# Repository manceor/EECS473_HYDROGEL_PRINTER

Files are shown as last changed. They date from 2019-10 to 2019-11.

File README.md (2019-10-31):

# Software Setup Guide

## Flashing the ATmega1284P through USB

To program the ATmega1284P, install download AVROSP.

This guide assumes that you have AVROSP added to your PATH.

1) When you first plug in the board

2) Hold RESET and SW0

3) Let go of RESET

4) Let go of SW0

5) In the terminal, enter the command "mode comx baud=57600 parity=n data=8".
    Replace the "x" in "comx" with the COM port that your board is plugged into.
    This can be found in the "Device Manager" on windows (AVR only supports COM ports 1-8)

6) In the folder where your .hex file is, run the following command:
    "AVROSP -dATmega1284P -cCOMx -pf -vf -if "filename.hex" -e".

## Setting up Atmel Studio for board programming

Install Atmel Studio 7

From fresh code:
Download TH3D Firmware <https://www.th3dstudio.com/knowledgebase/th3d-unified-firmware-package/>
Unzip into a folder of your choice, now referred to as "%TH3D DIRECTORY%"

1) New -> Project -> Create Project From Arduino Sketch

2) Create a new folder somewhere and select it

3) Sketch File:"%TH3D DIRECTORY%\TH3DUF_R2\Firmware\TH3DUF_R2\TH3DUF_R2.ino"

4) Arduino IDE Path: "%TH3D DIRECTORY%\TH3DUF_R2\Windows Arduino\"

5) To find the Marlin Code: see Arduino Core -> include -> variants

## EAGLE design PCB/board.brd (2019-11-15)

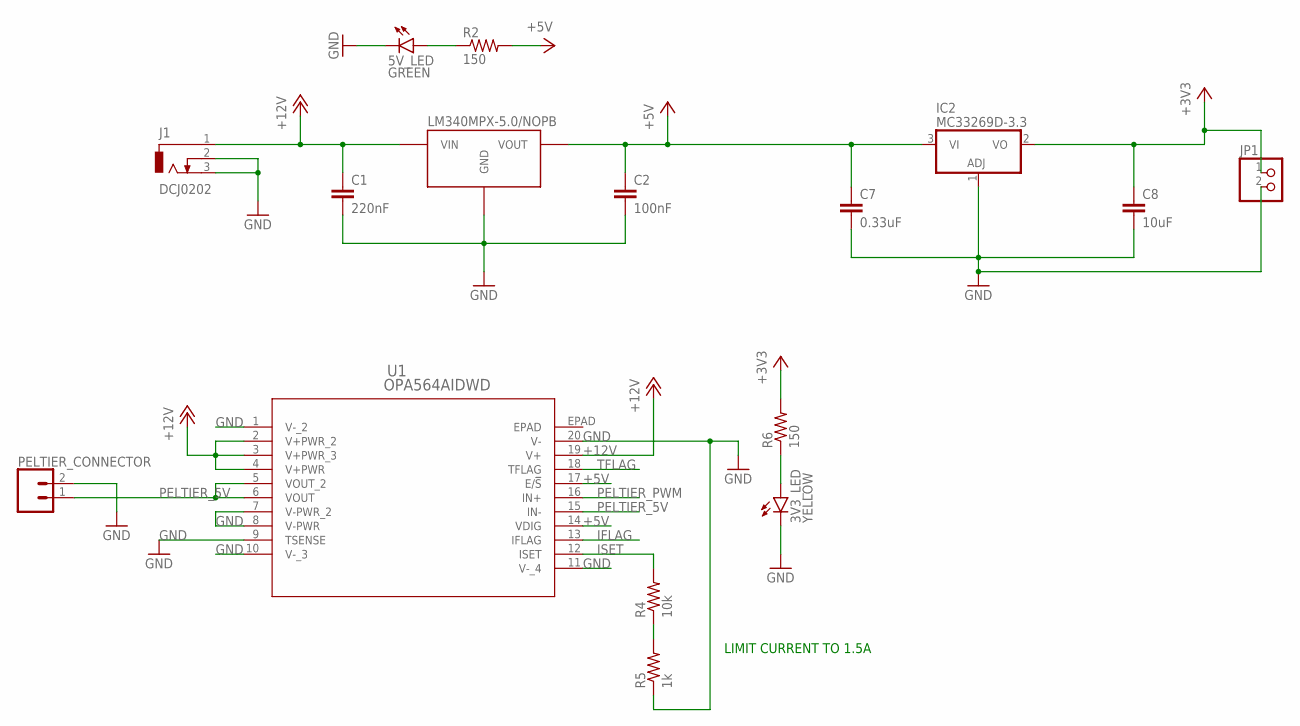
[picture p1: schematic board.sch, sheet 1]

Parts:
3V3_LED: YELLOW; CHIP-LED0603
5V_LED: GREEN; CHIP-LED0603
C1: 220nF; C0805
C2: 100nF; C0805
C7: 0.33uF; C0805
C8: 10uF; C0805
IC2: MC33269D-3.3; DPACK
J1: DCJ0202
JP1: PINHD-1X2; 1X02
LDO1: LM340MPX-5.0/NOPB; SOT-223
PELTIER_CONNECTOR: CONN_025MM; SCREWTERMINAL-5MM-2
R2, R6: 150; R0603
R4: 10k; R0603
R5: 1k; R0603
U1: OPA564AIDWD; DWD20_4P62X3P56

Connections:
+3V3: C8.1, IC2.2 (VO), JP1.1, R6.2
+5V: C2.1, C7.1, IC2.3 (VI), LDO1.P$3 (VOUT), R2.2, U1.14 (VDIG), U1.17 (E/!S); also elsewhere on the board
+12V: C1.1, J1.1, LDO1.P$1 (VIN), U1.2 (V+PWR_2), U1.3 (V+PWR_3), U1.4 (V+PWR), U1.19 (V+); also elsewhere on the board
GND: 3V3_LED.C, 5V_LED.C, C1.2, C2.2, C7.2, C8.2, IC2.1 (ADJ), J1.2, J1.3, JP1.2, LDO1.P$2 (GND), LDO1.P$4 (GND), PELTIER_CONNECTOR.2, R5.1, U1.1 (V-_2), U1.7 (V-PWR_2), U1.8 (V-PWR), U1.9 (TSENSE), U1.10 (V-_3), U1.11 (V-_4), U1.20 (V-); also elsewhere on the board
IFLAG: U1.13 (IFLAG); also elsewhere on the board
ISET: R4.2, U1.12 (ISET)
unnamed: 5V_LED.A, R2.1
unnamed: R4.1, R5.2
unnamed: 3V3_LED.A, R6.1
PELTIER_5V: PELTIER_CONNECTOR.1, U1.5 (VOUT_2), U1.6 (VOUT), U1.15 (IN-)
PELTIER_PWM: U1.16 (IN+); also elsewhere on the board
TFLAG: U1.18 (TFLAG); also elsewhere on the board

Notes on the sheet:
LIMIT CURRENT TO 1.5A

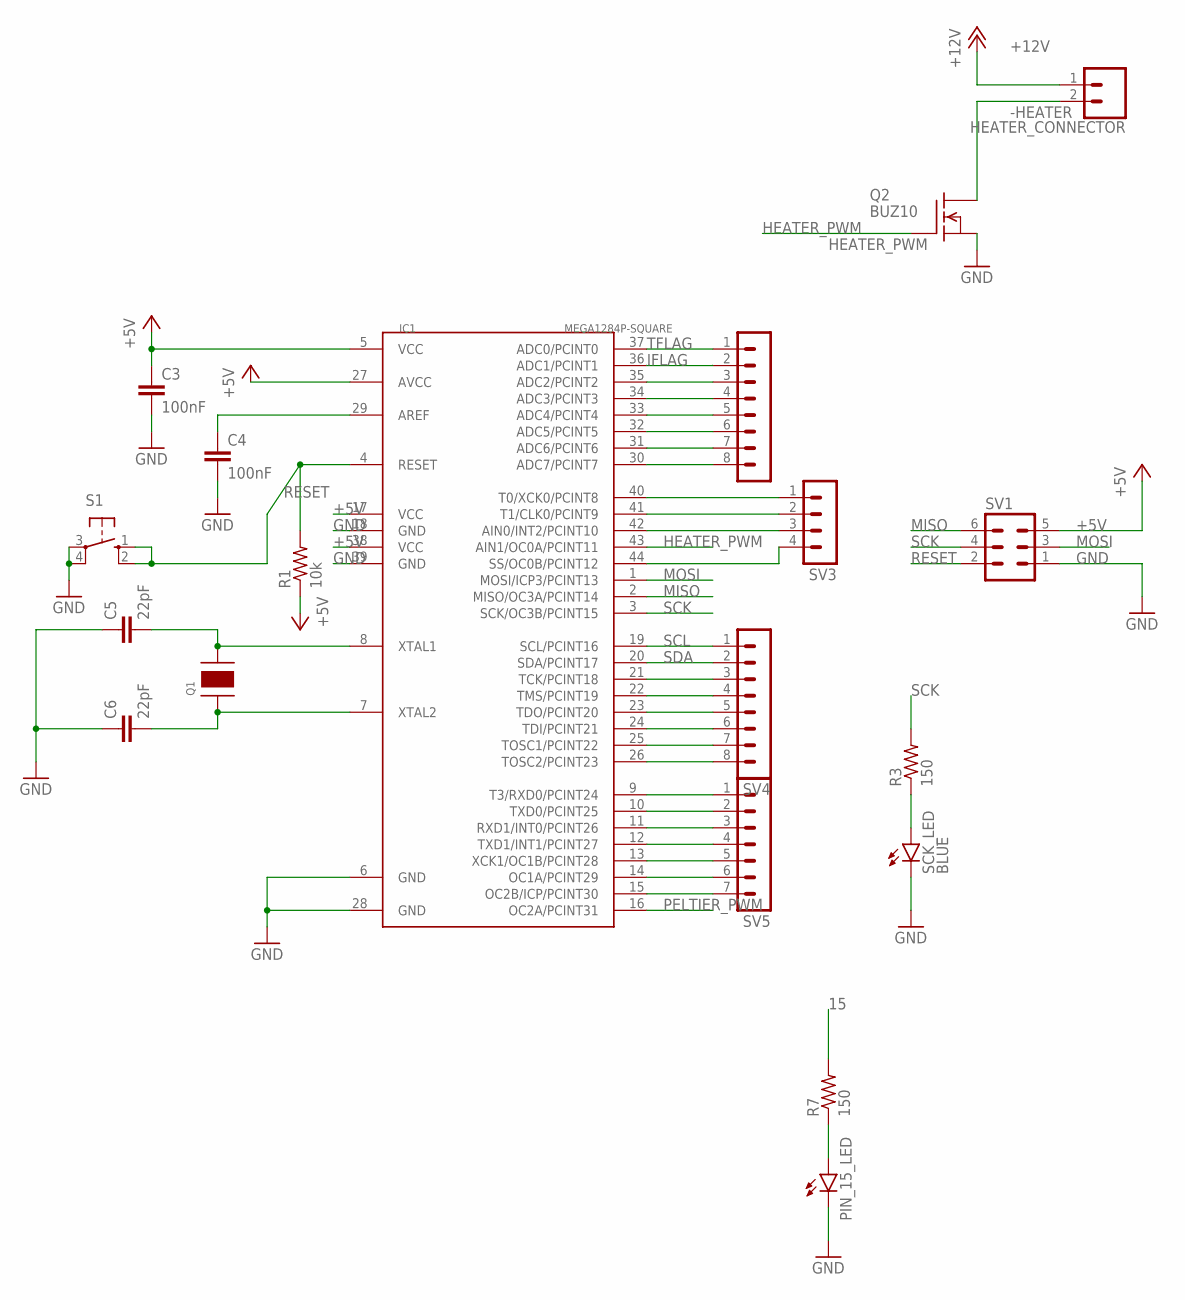
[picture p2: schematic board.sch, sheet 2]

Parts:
C3, C4: 100nF; C0603
C5, C6: 22pF; C0603
HEATER_CONNECTOR: CONN_025MM; SCREWTERMINAL-5MM-2
IC1: MEGA1284P-SQUARE; TQFP44
PIN_15_LED: BLUE; CHIP-LED0603
Q1: CRYSTAL_16MHZ_SMD; 4-SMD_DFN
Q2: BUZ10; TO220
R1: 10k; R0603
R3, R7: 150; R0603
S1: 10-XX; B3F-10XX
SCK_LED: BLUE; CHIP-LED0603
SV1: MA03-2
SV2, SV4: MA08-1
SV3: MA04-1
SV5: MA07-1

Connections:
9: IC1.9 (T3/RXD0/PCINT24), SV5.1
10: IC1.10 (TXD0/PCINT25), SV5.2
11: IC1.11 (RXD1/INT0/PCINT26), SV5.3
12: IC1.12 (TXD1/INT1/PCINT27), SV5.4
13: IC1.13 (XCK1/OC1B/PCINT28), SV5.5
14: IC1.14 (OC1A/PCINT29), SV5.6
15: IC1.15 (OC2B/ICP/PCINT30), R7.2, SV5.7
21: IC1.21 (TCK/PCINT18), SV4.3
22: IC1.22 (TMS/PCINT19), SV4.4
23: IC1.23 (TDO/PCINT20), SV4.5
24: IC1.24 (TDI/PCINT21), SV4.6
25: IC1.25 (TOSC1/PCINT22), SV4.7
26: IC1.26 (TOSC2/PCINT23), SV4.8
30: IC1.30 (ADC7/PCINT7), SV2.8
31: IC1.31 (ADC6/PCINT6), SV2.7
32: IC1.32 (ADC5/PCINT5), SV2.6
33: IC1.33 (ADC4/PCINT4), SV2.5
34: IC1.34 (ADC3/PCINT3), SV2.4
35: IC1.35 (ADC2/PCINT2), SV2.3
40: IC1.40 (T0/XCK0/PCINT8), SV3.1
41: IC1.41 (T1/CLK0/PCINT9), SV3.2
42: IC1.42 (AIN0/INT2/PCINT10), SV3.3
44: IC1.44 (SS/OC0B/PCINT12), SV3.4
+5V: C3.1, IC1.5 (VCC), IC1.17 (VCC), IC1.27 (AVCC), IC1.38 (VCC), R1.1, SV1.5; also elsewhere on the board
+12V: HEATER_CONNECTOR.1; also elsewhere on the board
-HEATER: HEATER_CONNECTOR.2, Q2.2 (D)
GND: C3.2, C4.2, C5.1, C6.1, IC1.6 (GND), IC1.18 (GND), IC1.28 (GND), IC1.39 (GND), PIN_15_LED.C, Q2.3 (S), S1.3, S1.4 (P1), SCK_LED.C, SV1.1; also elsewhere on the board
HEATER_PWM: IC1.43 (AIN1/OC0A/PCINT11), Q2.1 (G)
IFLAG: IC1.36 (ADC1/PCINT1), SV2.2; also elsewhere on the board
MISO: IC1.2 (MISO/OC3A/PCINT14), SV1.6
MOSI: IC1.1 (MOSI/ICP3/PCINT13), SV1.3
unnamed: PIN_15_LED.A, R7.1
unnamed: C4.1, IC1.29 (AREF)
unnamed: C5.2, IC1.8 (XTAL1), Q1.X2
unnamed: C6.2, IC1.7 (XTAL2), Q1.X1
unnamed: R3.1, SCK_LED.A
PELTIER_PWM: IC1.16 (OC2A/PCINT31); also elsewhere on the board
RESET: IC1.4 (RESET), R1.2, S1.1 (S), S1.2 (S1), SV1.2
SCK: IC1.3 (SCK/OC3B/PCINT15), R3.2, SV1.4
SCL: IC1.19 (SCL/PCINT16), SV4.1
SDA: IC1.20 (SDA/PCINT17), SV4.2
TFLAG: IC1.37 (ADC0/PCINT0), SV2.1; also elsewhere on the board

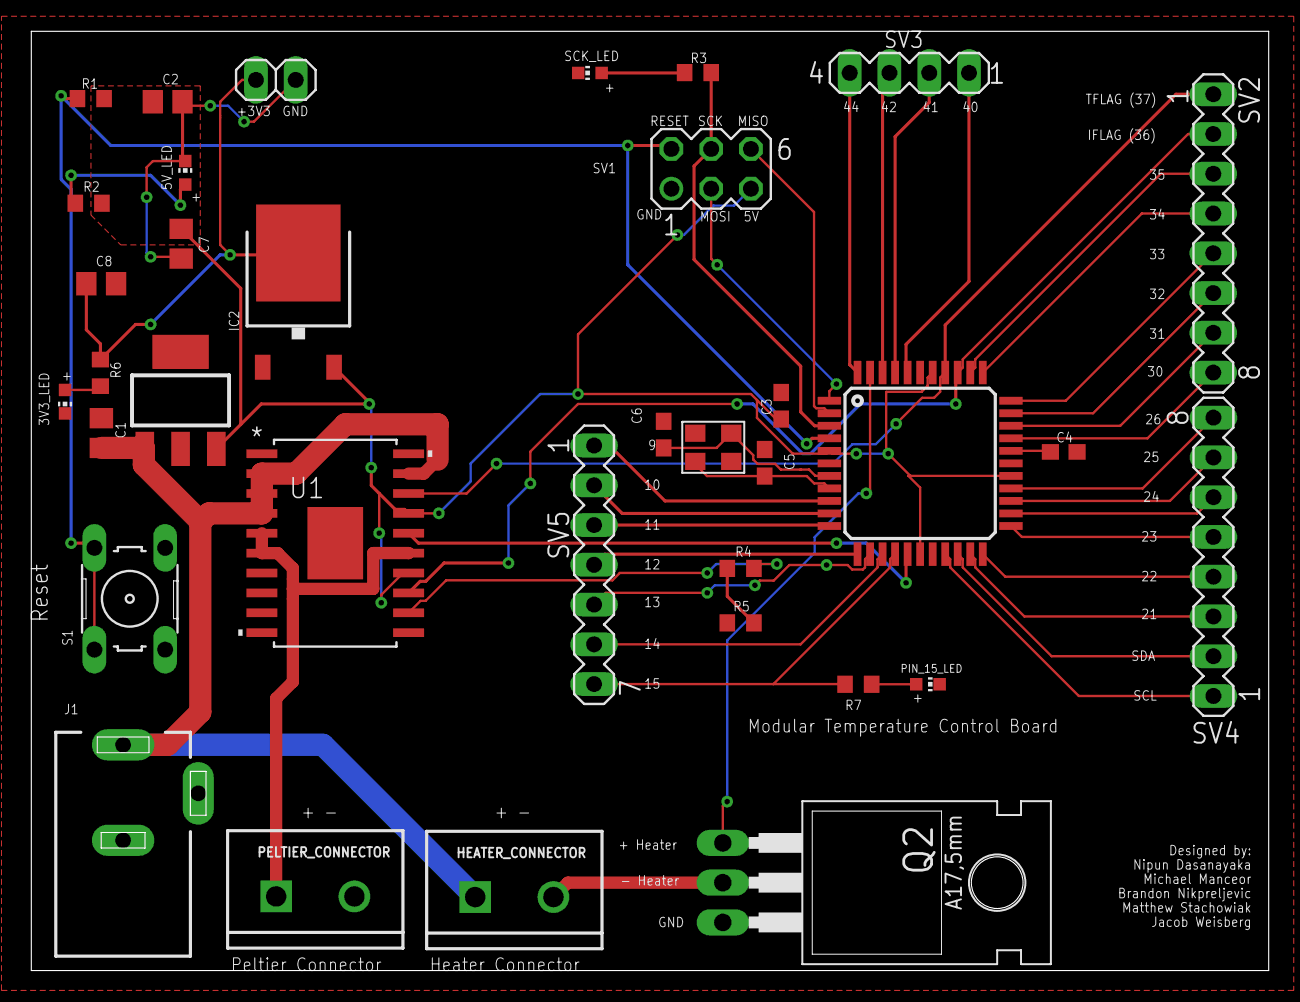
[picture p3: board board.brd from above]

Board: 2 copper layers, 79.0 x 60.0 mm, 35 parts (0 on the bottom side), 48 nets.

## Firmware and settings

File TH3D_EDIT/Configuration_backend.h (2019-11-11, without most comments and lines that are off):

#define CONFIGURATION_BACKEND_H
#define CONFIGURATION_BACKEND_H_VERSION 010109
#include "Configuration_th3d.h"
#if DISABLED(TH3DINHOUSEMACHINE)
  #if DISABLED(MKS_PRINTER)
    #if ENABLED(TMC_CREALITY_BOARD) || ENABLED(CR10S_PRO) || ENABLED(CR10_V2)
      #define X_DRIVER_TYPE  TMC2208_STANDALONE
      #define Y_DRIVER_TYPE  TMC2208_STANDALONE
      #define Z_DRIVER_TYPE  TMC2208_STANDALONE
      #define X2_DRIVER_TYPE A4988
      #define Y2_DRIVER_TYPE A4988
      #define Z2_DRIVER_TYPE A4988
      #define E0_DRIVER_TYPE TMC2208_STANDALONE
      #define E1_DRIVER_TYPE A4988
      #define E2_DRIVER_TYPE A4988
      #define E3_DRIVER_TYPE A4988
      #define E4_DRIVER_TYPE A4988
    #elif DISABLED(CUSTOM_DRIVERS)
      #define X_DRIVER_TYPE  A4988
      #define Y_DRIVER_TYPE  A4988
      #define Z_DRIVER_TYPE  A4988
      #define X2_DRIVER_TYPE A4988
      #define Y2_DRIVER_TYPE A4988
      #define Z2_DRIVER_TYPE A4988
      #define E0_DRIVER_TYPE A4988
      #define E1_DRIVER_TYPE A4988
      #define E2_DRIVER_TYPE A4988
      #define E3_DRIVER_TYPE A4988
      #define E4_DRIVER_TYPE A4988
    #endif
  #endif
#endif
#if ENABLED(CUSTOM_PROBE)
  #define EZABL_ENABLE
#endif
#if ENABLED(CR10V2_OEM)
  #define EZABL_ENABLE
  #define X_PROBE_OFFSET_FROM_EXTRUDER 52
  #define Y_PROBE_OFFSET_FROM_EXTRUDER 5
#endif
#if ENABLED(CR10S_PRO_OEM)
  #define EZABL_ENABLE
  #define X_PROBE_OFFSET_FROM_EXTRUDER -27
  #define Y_PROBE_OFFSET_FROM_EXTRUDER 0
#endif
#if ENABLED(WANHAO_I3_PLUS_EZABL)
  #define ADVi3PP_PROBE
  #define ADVi3PP_MARK2
  #define EZABL_ENABLE
  #define X_PROBE_OFFSET_FROM_EXTRUDER 0
  #define Y_PROBE_OFFSET_FROM_EXTRUDER 0
  #define Z_PROBE_OFFSET_FROM_EXTRUDER 0
#endif
#if ENABLED(TARANTULA_PRO_OEM)
  #define X_PROBE_OFFSET_FROM_EXTRUDER -65
  #define Y_PROBE_OFFSET_FROM_EXTRUDER 0
  #define EZABL_ENABLE
#endif
#if ENABLED(ENDER4_OEM_LEFT)
  #define X_PROBE_OFFSET_FROM_EXTRUDER -53
  #define Y_PROBE_OFFSET_FROM_EXTRUDER -19
  #define EZABL_ENABLE
#endif
#if ENABLED(ADIM_I3P_OEM)
  #define X_PROBE_OFFSET_FROM_EXTRUDER 33
  #define Y_PROBE_OFFSET_FROM_EXTRUDER -60
  #define EZABL_ENABLE
#endif
#if ENABLED(GEE_A10_V1_OEM)
  #define X_PROBE_OFFSET_FROM_EXTRUDER -54
  #define Y_PROBE_OFFSET_FROM_EXTRUDER 0
  #define EZABL_ENABLE
#endif
#if ENABLED(GEE_A10_V2_OEM)
  #define X_PROBE_OFFSET_FROM_EXTRUDER -52
  #define Y_PROBE_OFFSET_FROM_EXTRUDER 0
  #define EZABL_ENABLE
#endif
#if ENABLED(CR10_VOLCANO)
  #define X_PROBE_OFFSET_FROM_EXTRUDER 30
  #define Y_PROBE_OFFSET_FROM_EXTRUDER 12
  #define EZABL_ENABLE
#endif
#if ENABLED(CR10_V6HEAVYDUTY)
  #define X_PROBE_OFFSET_FROM_EXTRUDER 63
  #define Y_PROBE_OFFSET_FROM_EXTRUDER 0
  #define EZABL_ENABLE
#endif
#if ENABLED(EZ300_OEM_MOUNT)
  #define X_PROBE_OFFSET_FROM_EXTRUDER -32
  #define Y_PROBE_OFFSET_FROM_EXTRUDER -8
  #define EZABL_ENABLE
#endif
#if ENABLED(CR10_OEM)
  #define X_PROBE_OFFSET_FROM_EXTRUDER -44
  #define Y_PROBE_OFFSET_FROM_EXTRUDER -10
  #define EZABL_ENABLE
#endif
#if ENABLED(CR10_FANG) //DISCONTINUED - SAGS TOO MUCH
  #define X_PROBE_OFFSET_FROM_EXTRUDER 48
  #define Y_PROBE_OFFSET_FROM_EXTRUDER -11
  #define EZABL_ENABLE
#endif
#if ENABLED(TM3DAERO)
  #define X_PROBE_OFFSET_FROM_EXTRUDER -51
  #define Y_PROBE_OFFSET_FROM_EXTRUDER -7
  #define EZABL_ENABLE
#endif
#if ENABLED(TM3DAERO_EXTENDED)
  #define X_PROBE_OFFSET_FROM_EXTRUDER -55
  #define Y_PROBE_OFFSET_FROM_EXTRUDER -7
  #define EZABL_ENABLE
#endif
#if ENABLED(ENDER2_OEM)
  #define X_PROBE_OFFSET_FROM_EXTRUDER -33
  #define Y_PROBE_OFFSET_FROM_EXTRUDER -10
  #define EZABL_ENABLE
#endif
#if ENABLED(ENDER2_V6)
  #define X_PROBE_OFFSET_FROM_EXTRUDER -35
  #define Y_PROBE_OFFSET_FROM_EXTRUDER -2
  #define EZABL_ENABLE
#endif
#if ENABLED(TORNADO_OEM)
  #define X_PROBE_OFFSET_FROM_EXTRUDER -37
  #define Y_PROBE_OFFSET_FROM_EXTRUDER -10
  #define EZABL_ENABLE
#endif
#if ENABLED(TORNADO_VOLCANO)
  #define X_PROBE_OFFSET_FROM_EXTRUDER 30
  #define Y_PROBE_OFFSET_FROM_EXTRUDER 12
  #define EZABL_ENABLE
#endif
#if ENABLED(TORNADO_V6HEAVYDUTY)
  #define X_PROBE_OFFSET_FROM_EXTRUDER 63
  #define Y_PROBE_OFFSET_FROM_EXTRUDER 0
  #define EZABL_ENABLE
#endif
#if ENABLED(TAZ5_OEM)
  #define X_PROBE_OFFSET_FROM_EXTRUDER -52
  #define Y_PROBE_OFFSET_FROM_EXTRUDER 15
  #define EZABL_ENABLE
#endif
#if ENABLED(WANHAO_I3_OEM)
  #define X_PROBE_OFFSET_FROM_EXTRUDER -25
  #define Y_PROBE_OFFSET_FROM_EXTRUDER -38
  #define EZABL_ENABLE
#endif
#if ENABLED(WANHAO_D6_OEM)
  #define X_PROBE_OFFSET_FROM_EXTRUDER 24
  #define Y_PROBE_OFFSET_FROM_EXTRUDER -16
  #define EZABL_ENABLE
#endif
#if ENABLED(WANHAO_I3_DIIICOOLER)
  #define X_PROBE_OFFSET_FROM_EXTRUDER -36
  #define Y_PROBE_OFFSET_FROM_EXTRUDER -37
  #define EZABL_ENABLE
#endif
#if ENABLED(WANHAO_I3MINI_OEM_EZABLMINI)
  #define X_PROBE_OFFSET_FROM_EXTRUDER -32
  #define Y_PROBE_OFFSET_FROM_EXTRUDER 0
  #define EZABL_ENABLE
#endif
#if ENABLED(WANHAO_I3MINI_OEM)
  #define X_PROBE_OFFSET_FROM_EXTRUDER -36
  #define Y_PROBE_OFFSET_FROM_EXTRUDER 0
  #define EZABL_ENABLE
#endif
#if ENABLED(PETSFANG)
  #define X_PROBE_OFFSET_FROM_EXTRUDER 48
  #define Y_PROBE_OFFSET_FROM_EXTRUDER -2
  #define EZABL_ENABLE
#endif
#if ENABLED(ALFAWISEU10_OEM)
  #define X_PROBE_OFFSET_FROM_EXTRUDER 39
  #define Y_PROBE_OFFSET_FROM_EXTRUDER -47
  #define EZABL_ENABLE
#endif
#if ENABLED(ALFAWISEU10_PETSFANG)
  #define X_PROBE_OFFSET_FROM_EXTRUDER -48
  #define Y_PROBE_OFFSET_FROM_EXTRUDER -2
  #define EZABL_ENABLE
#endif
#if ENABLED(ANET_OEM)
  #define EZABL_ENABLE
#endif
#if ENABLED(CR10_V2)
    #define MOTHERBOARD BOARD_CR10S
  #define REPRAP_DISCOUNT_FULL_GRAPHIC_SMART_CONTROLLER
  #define BAUDRATE 115200
  #define X_MIN_ENDSTOP_INVERTING false
  #define Y_MIN_ENDSTOP_INVERTING false
  #define Z_MIN_ENDSTOP_INVERTING false
  #define X_MAX_ENDSTOP_INVERTING false
  #define Y_MAX_ENDSTOP_INVERTING false
  #define Z_MAX_ENDSTOP_INVERTING false
  #define Z_MIN_PROBE_ENDSTOP_INVERTING false
  #if ENABLED(TITAN_EXTRUDER)
    #define DEFAULT_AXIS_STEPS_PER_UNIT   { 80, 80, 400, TITAN_EXTRUDER_STEPS }
  #else
    #if ENABLED(CUSTOM_ESTEPS)
      #define DEFAULT_AXIS_STEPS_PER_UNIT   { 80, 80, 400, CUSTOM_ESTEPS_VALUE }
    #else
      #define DEFAULT_AXIS_STEPS_PER_UNIT   { 80, 80, 400, 93 }
    #endif
  #endif
  #define DEFAULT_MAX_FEEDRATE          { 500, 500, 15, 50 }
  #define DEFAULT_MAX_ACCELERATION      { 1000, 1000, 100, 1000 }
  #define DEFAULT_ACCELERATION          500
  #define DEFAULT_RETRACT_ACCELERATION  1000
  #define DEFAULT_TRAVEL_ACCELERATION   500
  #define DEFAULT_XJERK                  8.0
  #define DEFAULT_YJERK                  8.0
  #define DEFAULT_ZJERK                  0.4
  #define DEFAULT_EJERK                  5.0
  #define INVERT_X_DIR false
  #define INVERT_Y_DIR false
  #define INVERT_Z_DIR true
  #if ENABLED(TITAN_EXTRUDER)
    #define INVERT_E0_DIR true
  #else
    #define INVERT_E0_DIR false
  #endif
  #define X_BED_SIZE 300
  #define Y_BED_SIZE 300
  #define Z_MAX_POS 400
  #if ENABLED(HOME_ADJUST)
    #define X_MIN_POS X_HOME_ADJUST_LOCATION
    #define Y_MIN_POS Y_HOME_ADJUST_LOCATION
  #else
    #define X_MIN_POS 0
    #define Y_MIN_POS 0
  #endif
  #define PRINTER_ENABLED_CHECK
#endif //end cr-10 v2 settings
#if ENABLED(CR10S_PRO)
  #ifndef MOTHERBOARD
    #define MOTHERBOARD BOARD_CR10S
  #endif
  #if ENABLED(RR_LCD_UPGRADE)
    #define REPRAP_DISCOUNT_FULL_GRAPHIC_SMART_CONTROLLER
  #endif
  #define BAUDRATE 115200
  #define X_MIN_ENDSTOP_INVERTING false
  #define Y_MIN_ENDSTOP_INVERTING false
  #define Z_MIN_ENDSTOP_INVERTING false
  #define X_MAX_ENDSTOP_INVERTING false
  #define Y_MAX_ENDSTOP_INVERTING false
  #define Z_MAX_ENDSTOP_INVERTING false
  #define Z_MIN_PROBE_ENDSTOP_INVERTING false
  #if ENABLED(TITAN_EXTRUDER)
    #define DEFAULT_AXIS_STEPS_PER_UNIT   { 80, 80, 400, TITAN_EXTRUDER_STEPS }
  #else
    #if ENABLED(CUSTOM_ESTEPS)
      #define DEFAULT_AXIS_STEPS_PER_UNIT   { 80, 80, 400, CUSTOM_ESTEPS_VALUE }
    #else
      #define DEFAULT_AXIS_STEPS_PER_UNIT   { 80, 80, 400, 140 }
    #endif
  #endif
  #define DEFAULT_MAX_FEEDRATE          { 500, 500, 15, 50 }
  #define DEFAULT_MAX_ACCELERATION      { 1000, 1000, 100, 1000 }
  #define DEFAULT_ACCELERATION          500
  #define DEFAULT_RETRACT_ACCELERATION  1000
  #define DEFAULT_TRAVEL_ACCELERATION   500
  #define DEFAULT_XJERK                  8.0
  #define DEFAULT_YJERK                  8.0
  #define DEFAULT_ZJERK                  0.4
  #define DEFAULT_EJERK                  5.0
  #define INVERT_X_DIR false
  #define INVERT_Y_DIR true
  #define INVERT_Z_DIR true
  #if ENABLED(TITAN_EXTRUDER)
    #define INVERT_E0_DIR true
  #else
    #define INVERT_E0_DIR false
  #endif
  #define X_BED_SIZE 300
  #define Y_BED_SIZE 300
  #define Z_MAX_POS 400
  #define REVERSE_ENCODER_DIRECTION
  #if ENABLED(HOME_ADJUST)
    #define X_MIN_POS X_HOME_ADJUST_LOCATION
    #define Y_MIN_POS Y_HOME_ADJUST_LOCATION
  #else
    #define X_MIN_POS 0
    #define Y_MIN_POS 0
  #endif
  #define ENCODER_PULSES_PER_STEP 1
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

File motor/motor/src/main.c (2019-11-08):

/**
 * \file
 *
 * \brief Empty user application template
 *
 */

/**
 * \mainpage User Application template doxygen documentation
 *
 * \par Empty user application template
 *
 * Bare minimum empty user application template
 *
 * \par Content
 *
 * -# Include the ASF header files (through asf.h)
 * -# "Insert system clock initialization code here" comment
 * -# Minimal main function that starts with a call to board_init()
 * -# "Insert application code here" comment
 *
 */

/*
 * Include header files for all drivers that have been imported from
 * Atmel Software Framework (ASF).
 */
/*
 * Support and FAQ: visit <a href="https://www.microchip.com/support/">Microchip Support</a>
 */
#include <asf.h>
#include <avr/io.h>

void initGPIO(void);
void setMotorDir(bool);
void moveMotor(int);
void setSpeed(int);
void motorSleep(bool);
void motorReset(void);
void setStepDiv(int);
void setEnable(bool);

int pulseDelay = 750;

int main (void)
{
	/* Insert system clock initialization code here (sysclk_init()). */

	board_init();
	/* Insert application code here, after the board has been initialized. */
	initGPIO();
	
	//change stuff below; SW0 = PB0 = PCINT8
	//PCMSK0 |= (1<<PCINT0); //enable PCINT0
	//PCIFR |= (1<<PCIF0); //clear PCINT0
	//PCICR |= (1<<PCIE0); //enable PCINT0
	
	sei(); //enable interrupts
	int dir = 0;
	setStepDiv(1);
	setEnable(true);
	motorSleep(true); //active low, so this keeps it awake
	while(1){
		for(int i = 0; i < 20000; ++i){
			moveMotor(1);
		}
		dir = !dir;
		setMotorDir(dir);
		delay_ms(50);
	}
}

void initGPIO(){
	DDRB = (1<<DDB0) | (1<<DDB1) | (1<<DDB2) | (1<<DDB3); //set GPIO0 through GPIO3 as outputs
	DDRD |= (1<<DDD4) | (1<<DDD5); //enable GPIO4 and GPIO5 as outputs
	DDRC |= (1<<DDC4) | (1<<DDC5); //enable GPIO6 and GPIO7 as outputs
	
	PORTB |= (1<<PORTB3); //set reset high since it is active low
}

void setMotorDir(bool dir){
	//using GPIO0 (PORTB0) for pulse dir
	if(dir){
		PORTB |= (1<<PORTB0);
	}
	else{
		PORTB &= ~(1<<PORTB0);
	}
}

void moveMotor(int steps){
	//using GPIO1 (PORTB1) for step
	PORTB |= (1<<PORTB1);
	delay_us(pulseDelay);
	PORTB &= ~(1<<PORTB1);
	delay_us(pulseDelay);
}

void setSpeed(int speed){
	if(speed < 50){
		pulseDelay = 250;
	}
	else{
		pulseDelay = 750;
	}
}

void motorSleep(bool set){
	//using GPIO2 (PORTB2) for sleep
	//active low
	if(set){
		PORTB |= (1<<PORTB2);
	}
	else{
		PORTB &= ~(1<<PORTB2);
	}
}

void motorReset(){
	//using GPIO3 (PORTB3) for reset
	//active low
	PORTB &= ~(1<<PORTB3);
	delay_us(50);
	PORTB |= (1<<PORTB3);
	return;
}

//Change the microstepping division. Takes effect on next STEP pulse.
void setStepDiv(int div){
	//using GPIO4 (PORTD4) as MS3
	//using GPIO5 (PORTD5) as MS2
	//using GPIO6 (PORTC4) as MS1
	switch(div){ //consider stopping motor while changing settings
		case 1: //full step
			PORTD &= ~(1<<PORTD4); //0
			PORTD &= ~(1<<PORTD5); //0
			PORTC &= ~(1<<PORTC4); //0
			break;
		case 2: //half step
			PORTD &= ~(1<<PORTD4); //0
			PORTD &= ~(1<<PORTD5); //0
			PORTC |= (1<<PORTC4);  //1
			break;
		case 4:
			PORTD &= ~(1<<PORTD4); //0
			PORTD |= (1<<PORTD5);  //1
			PORTC &= ~(1<<PORTC4); //0
			break;
		case 8:
			PORTD &= ~(1<<PORTD4); //0
			PORTD |= (1<<PORTD5);  //1
			PORTC |= (1<<PORTC4);  //1
			break;
		case 16:
			PORTD |= (1<<PORTD4);  //1
			PORTD |= (1<<PORTD5);  //1
			PORTC |= (1<<PORTC4);  //1
			break;
		default: //not one of the supported options; maybe return an error msg
			break;
	}
	return;
}

void setEnable(bool set){
	if(set){
		PORTC |= (1<<PORTC5);
	}
	else{
		PORTC &= ~(1<<PORTC5);
	}
}

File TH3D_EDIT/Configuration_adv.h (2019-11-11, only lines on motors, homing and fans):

#define E1_AUTO_FAN_PIN -1
#define E2_AUTO_FAN_PIN -1
#define E3_AUTO_FAN_PIN -1
#define E4_AUTO_FAN_PIN -1
#define X_HOME_BUMP_MM 5
#define Y_HOME_BUMP_MM 5
#define Z_HOME_BUMP_MM 2
#define QUICK_HOME
#define MICROSTEP_MODES {16,16,16,16,16} // [1,2,4,8,16]
#define ADVANCED_PAUSE_FEATURE
  #define ADVANCED_PAUSE_PURGE_FEEDRATE        3
  #define ADVANCED_PAUSE_PURGE_LENGTH         50

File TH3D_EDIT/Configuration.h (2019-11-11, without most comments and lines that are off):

#define CONFIGURATION_H
#define CONFIGURATION_H_VERSION 010109
#define ENDER3
#define MKS_X_SIZE 300
#define MKS_Y_SIZE 300
#define MKS_Z_SIZE 300
#define MKS_X_ENDSTOP 0
#define MKS_Y_ENDSTOP 0
#define MKS_Z_ENDSTOP 0
#define X_HOME_LOCATION 0
#define Y_HOME_LOCATION 0
#define MKS_X_STEPS 80
#define MKS_Y_STEPS 80
#define MKS_Z_STEPS 400
#define MKS_E0_STEPS 95
#define MKS_E1_STEPS 95
#define MKS_X_DIRECTION 0
#define MKS_Y_DIRECTION 0
#define MKS_Z_DIRECTION 0
#define MKS_E0_DIRECTION 0
#define MKS_E1_DIRECTION 0
#define MKS_X_DRIVER TMC2208_STANDALONE
#define MKS_Y_DRIVER TMC2208_STANDALONE
#define MKS_Z_DRIVER A4988
#define MKS_E0_DRIVER A4988
#define MKS_E1_DRIVER A4988
#define MKS_E_THERMISTOR 1
#define MKS_BED_THERMISTOR 1
#define EZABL_POINTS 3
#define EZABL_PROBE_EDGE 15
#define EZABL_FASTPROBE
#define EZABL_OUTSIDE_GRID_COMPENSATION
#define CUSTOM_ESTEPS
#define CUSTOM_ESTEPS_VALUE 95
#define TITAN_EXTRUDER_STEPS 463
#define DUAL_HOTEND_X_DISTANCE 18.0
#define HOTEND_THERMAL_PROTECTION_TIME 60
#define BED_THERMAL_PROTECTION_TIME 180
#define X_HOME_ADJUST_LOCATION -10
#define Y_HOME_ADJUST_LOCATION -10
#define LINEAR_ADVANCE_K 0
#define LCD_LANGUAGE en
#include "Configuration_beta.h"
#include "Configuration_backend.h"
#define UNIFIED_VERSION "TH3D U1.R2.16a"

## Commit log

2019-10-20 initial motor driver files with Arduino code
2019-10-21 added Atmel Studio 7 project containing motor code that works on the ATmega1284P
    [motor.componentinfo.xml]
2019-10-21 Fixed gitignore tracking vs settings
    [motor.componentinfo.xml]
2019-10-21 motor updates
2019-10-24 Upload New File
    [Configuration.h]
2019-10-29 updated motor files for new controller
2019-11-07 Adding starter PCB files
    [board.brd, board.sch]
2019-11-07 Adding TH3D Edits
    [Configuration.h, Configuration_adv.h, Configuration_backend.h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]
2019-11-08 updated PCB with new LDO and PCB footprint
    [Configuration.h, Configuration_adv.h, Configuration_backend.h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]
2019-11-11 Fixed PCB stuff - main looking clean
    [main.cpp]
2019-11-11 Fixed 3d Printing
    [Configuration.h, Configuration_adv.h, Configuration_backend.h]
2019-11-11 Added Op-Amp for peltier control and MOSFET for hot end cartridge heater control
    [board.sch]
2019-11-11 Adding simple Gcode and preheat material lcd cmds
    [Configuration_backend.h]
2019-11-11 Added MOSFET for peltier control
    [board.brd, board.sch]
2019-11-11 Finished connections for op-amp
    [board.brd, board.sch]
2019-11-11 Fixed mosfet
    [board.brd, board.sch]
2019-11-11 Added connector for heater
    [board.brd, board.sch]
2019-11-12 Placing on board
    [board.brd, board.sch]
2019-11-12 started routing
    [board.brd]
2019-11-12 finished routing PCB
    [board.brd]
2019-11-12 finished routing PCB with added pins; need silkscreen!
    [board.brd, board.sch]
2019-11-14 Michael and Matthew, Silkscreening done
    [board.brd, board.sch]
2019-11-14 Gerber Files Generated
2019-11-14 Finalized Board #1
    [board.brd, board.sch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]
2019-11-15 Made some adjustments to silkscreen placement
    [board.brd]

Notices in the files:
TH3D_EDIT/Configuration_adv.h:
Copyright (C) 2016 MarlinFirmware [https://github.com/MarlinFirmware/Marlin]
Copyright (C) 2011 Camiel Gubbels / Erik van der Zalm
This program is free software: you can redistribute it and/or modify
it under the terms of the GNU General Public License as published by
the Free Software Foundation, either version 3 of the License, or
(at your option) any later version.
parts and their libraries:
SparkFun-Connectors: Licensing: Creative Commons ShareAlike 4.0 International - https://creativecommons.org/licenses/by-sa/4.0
